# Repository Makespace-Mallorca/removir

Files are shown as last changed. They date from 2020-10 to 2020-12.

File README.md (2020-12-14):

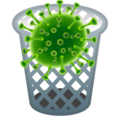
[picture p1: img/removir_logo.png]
#  RemoVir   

## Este repositorio contiene todos los recursos: instrucciones, código, documentación y datos para ayudarte a reciclar un Split (evaporador interior de aire acondicionado) a un eficiente filtro HEPA

Podrás montar un **purificador de aire con filtro HEPA** por poco más del coste de los filtros y lo más importante. Ayudarás a mantener el medio ambiente mientras proteges del contagio de COVID-19 el espacio que más necesites.

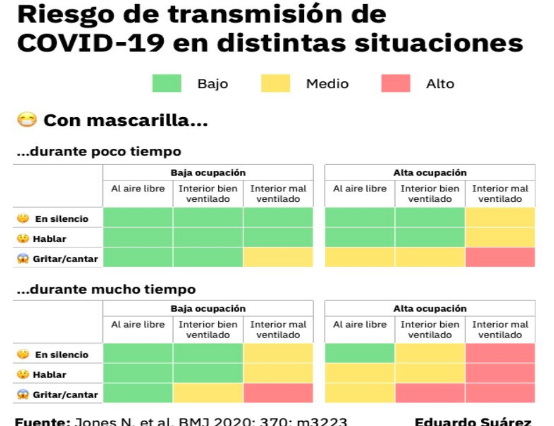
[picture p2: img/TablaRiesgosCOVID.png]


```text
Hemos querido enfocar nuestros esfuerzos a este tipo 
de dispositivos porque creemos que pueden ser una 
importante ayuda a evitar contagios. Las últimas 
evidencias científicas demuestran la transmisión de 
virus por aerosoles, es decir, por el mismo hecho de 
respirar. Esto aumenta el nivel de COV (Compuestos 
Orgánicos Volátiles entre los que se encuentra el 
virus SARS-CoV-2) algo que va correlacionado con la 
concentración de CO2. Esta evidencia hace necesaria 
una correcta ventilación de los espacios cerrados. 
Lo que es tan importante como mantener una distancia 
mínima.
```
<br>
<br>
<br>

Este proyecto parte de la iniciativa de Ernesto Gutiérrez [@erguro1973](https://twitter.com/erguro1973), de [Carlos Orts](https://github.com/McOrts) [@mcorts](https://twitter.com/mcorts) y de los asistentes a varios talleres realizados en el [Fablab de Mallorca](http://fablabmallorca.com/) y organizados por la [Asociación de Makers Mallorca](https://makespacemallorca.org/).

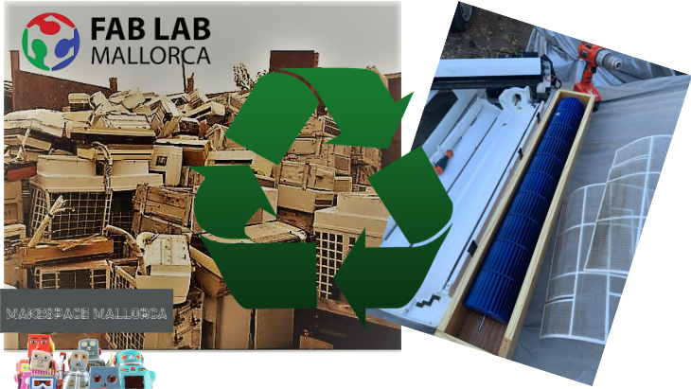
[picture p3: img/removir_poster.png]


**¿Con que vamos a trabajar?**
* Análisis de dinámica de fluidos.
* Control de motores.
* Uso de filtros HEPA.
* Programación C++ e IDE de Arduino
* Microcontroladores ESP8266.
* Sensores
* Comunicaciones MQTT
<br>

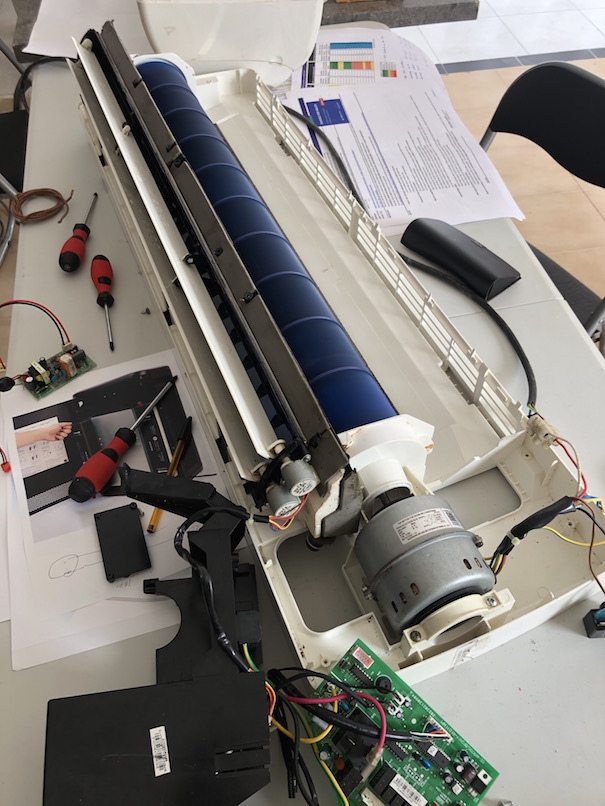
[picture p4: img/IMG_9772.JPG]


## Primer RemoVir, un _Mínimo Producto Viable_
Hemos trabajado sobre un Split marca Mundo Clima. Que ha resultado muy adecuado tanto para la sustitución de la electrócnica como para acomodar los filtros HEPA. Aunque se trata de un MPV. pretendemos que alcance un nivel H13 o superior según el estándar europeo EN 1822-1:2009. para ello se van a instalar 3 filtros HEPA H13 de un equipo profesional Honeywell Incorporaremos un completo sistemas de medición de calidad de aire, CO2, COV, temperatura, humedad y presión atmosférica de manera que sea capaz de adaptar su funcionamiento a las condiciones detectadas.

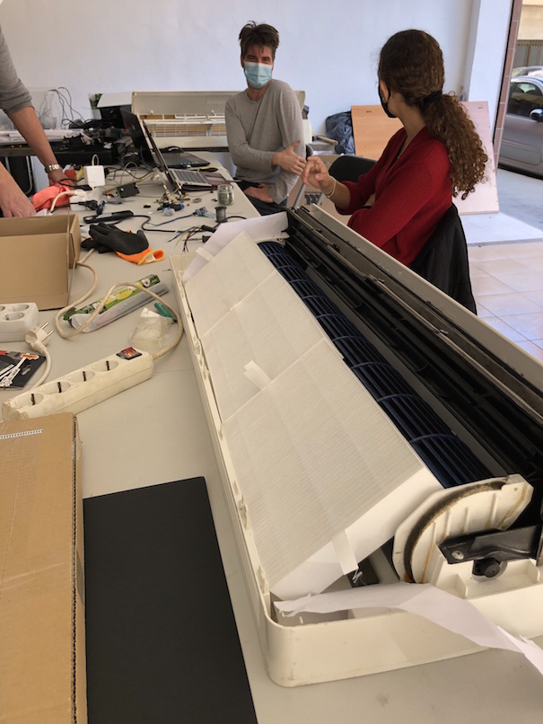
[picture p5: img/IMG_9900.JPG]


### Filtro HEPA (High Efficiency Particulate Air)
Un filtro HEPA funciona con diferentes principios. Lo que determina el comportamiento de la parte impulsora de aire. Una regla básica a tener en cuenta es que una mayor presión de aire puede bajar la eficiencia en la captura de componentes muy pequeños como virus.
El producto elegido ha sido el modelo empleado en el purificador profesional Honeywell H300 que incorpora filtros HEPA de grado H13
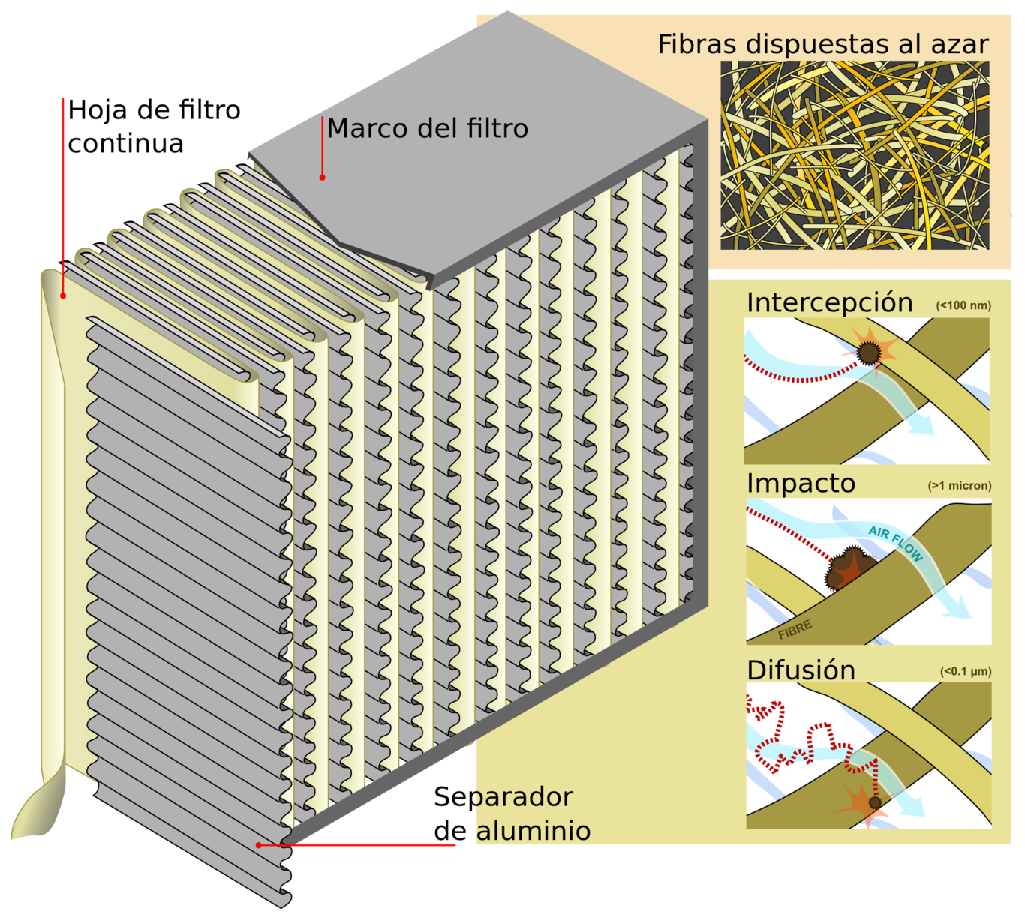
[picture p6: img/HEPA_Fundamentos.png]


### Electrónica
Se ha planteado utilizar el WEMOS D1 MINI Pro. Que es un procesador tipo ESP8266 de 16 bits con programación nativa en C++.
El borrador del esquemático de momento es este:
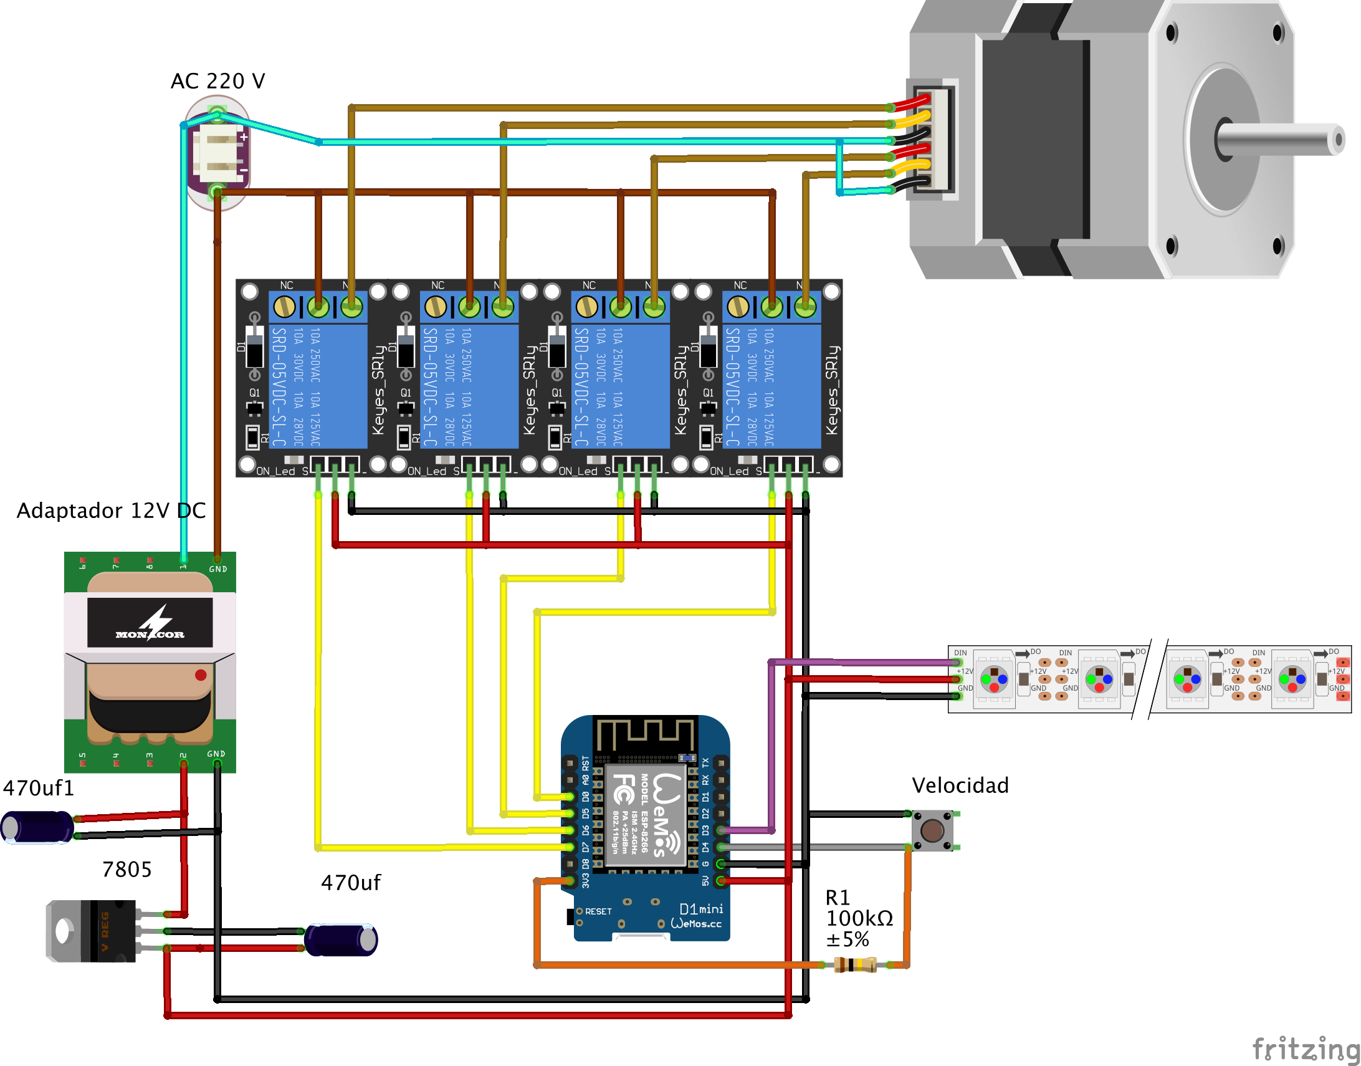
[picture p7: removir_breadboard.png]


### Estructura
Hay que tener en cuenta que detro de un Split encontraremos un ´evaporizador´. A todos los efectos es un radiador de aluminio que sin formar parte de la estructura del aparato. Le confiere uan rigidez estructural que perderemos si no acomodamos los filtros HEPA teniendo en cuenta esta doble función. El diseño de las piezas adicionales evidentemente es una caso diferente para cada modelo. 
Como ejemplo de cómo hacerlo, se han usado patrones en cartulina que luego se han modelizado en SolidWorks para acabar imprimiendolos en 3D de filamento. Los ficheros podéis encontrarlos en este mismo repo.

### Flujo de aire
Este es un concepto que hay que tener presente durante todo el rediseño del equipo. Tanto en el aspecto de caudal como el de presión. Una cosa el el volumen de aire por hora que podamos hacer pasar el equipo y otra diferente es la presión que el ventilador pueda aplicar al aire que mueve. Evidentemente ambos parámetros se ven disminuidos respecto al modelo de aire acondicionado original al sustituir el evaporizador por los filtro HEPA que ofrecen mucha más resistencia al paso del aire.
No está de más valorar las modificaciones haciendo sencillas pruebas de flujo como esta:
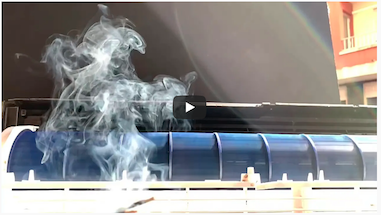
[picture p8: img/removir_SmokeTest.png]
RemoVir RealSmokeTest (https://youtu.be/LHWRh8wFhkA)


### Montaje
El proceso de adaptación y transformación de la mecánica y la electrónica, es algo laborioso y nos ha ocupado algunas semanas. 
* Por una parte hemos tenido que resolver el problema de la sujección mecánica de los filtros en el lugar dejado por el elemento evaporador de aluminio. En un principio de diseñaron soportes imprimibles en 3D par los elementos perpendiculares. Ya que los para las piezas transversales, el material impreso no tienen la rigidez suficiente. Empezamos a utilizar tablero DM que finalmente se ha usado para todo:
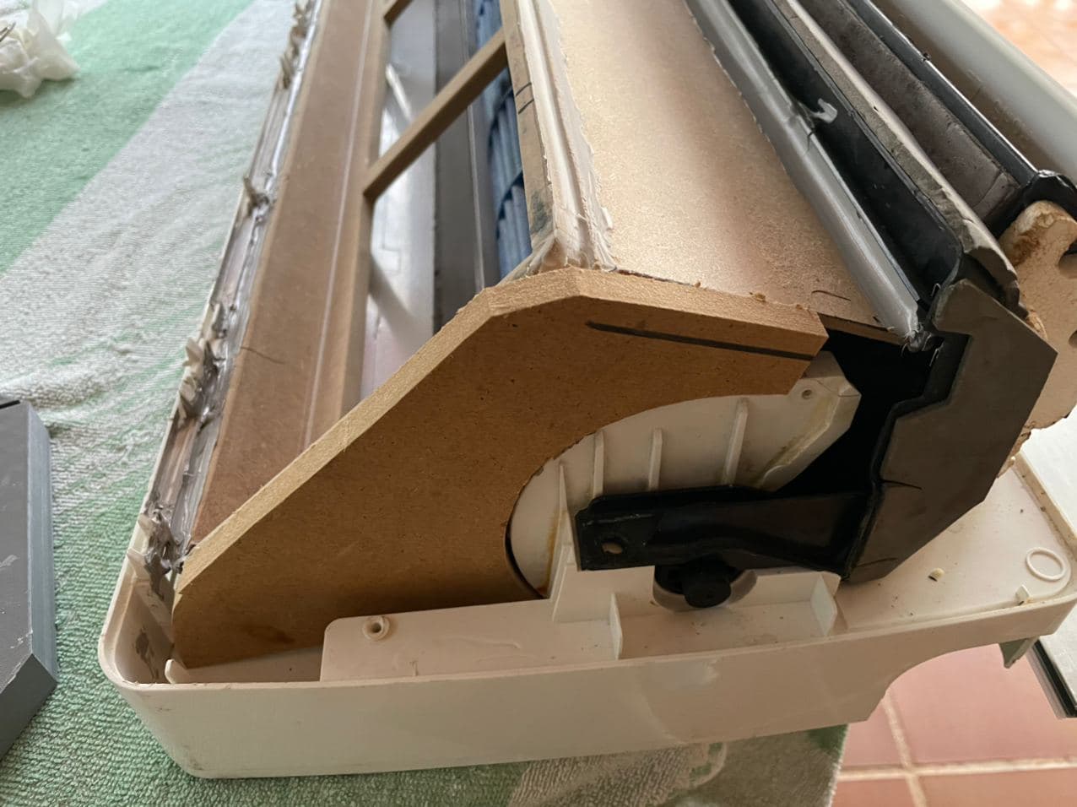
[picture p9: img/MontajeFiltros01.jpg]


* En la parte electrónica se ha utilizado la fuente de alimentación original adaptando la tensión con reguladores de tensión. La lógica está programada en C++ corriendo en un microcesador tipo ESP8266 utilizando las mínimas librerias y un solo bloque de código. Aún así el control se puede hacer desde una página web servida directamente por el micro WEMOS D1 Mini PRO a modo de punto de acceso Wifi.
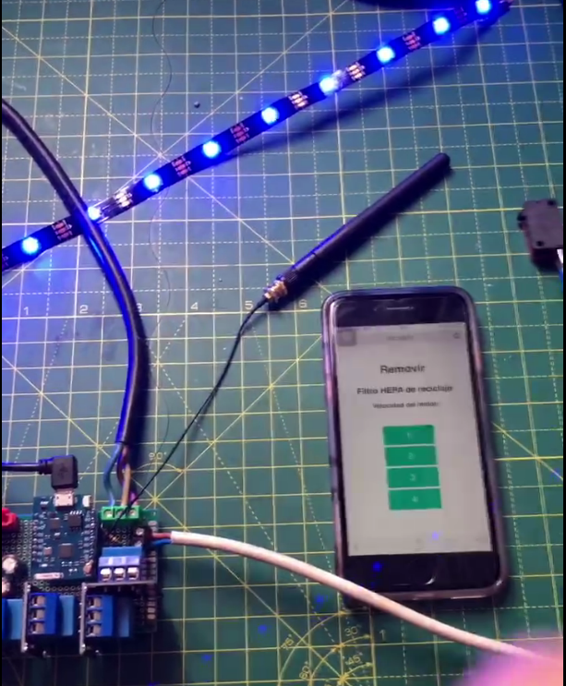
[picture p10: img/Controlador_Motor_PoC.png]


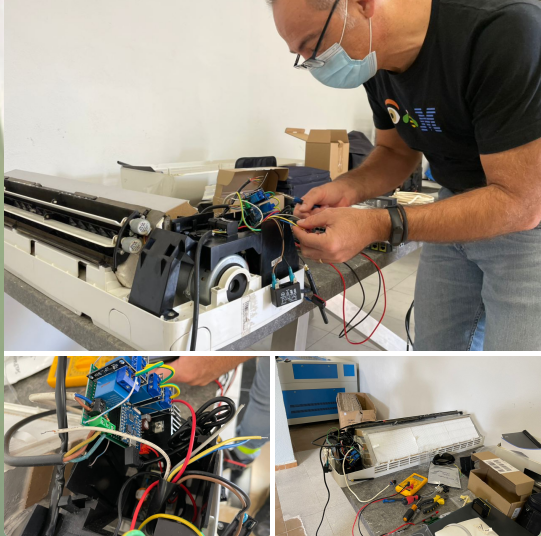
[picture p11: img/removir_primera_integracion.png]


### Primera integración y prueba
El segundo sábado de diciembre, en una de las mañanas de _cacharrero_ organizadas por el Fablab de Mallorca. Hemos integrado todos los componentes y hecho la primera prueba de arranque del motor. Las sensaciones han sido buenas. Un nivel de ruido aceptable así como un caudal de salida de aire aparentemente bueno.
La electrónica parece que está afectada por interferencias que han deshabilitado la conexión wifi en algunos momentos. Y ha detectado falsas pulsaciones en el control manual. Vamos a sustiuir microprocesador, el WEMOS D1 Mini PRO por un WEMOS D1 Mini con encapsulaciento.

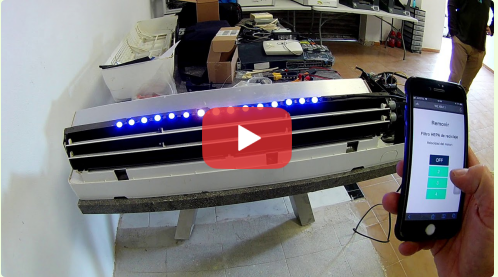
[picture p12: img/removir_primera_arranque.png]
RemoVir primer arranque (https://youtu.be/MKbnKUOGmzY)


### Mediciones y certificación
Como nos gusta saber si el trabajo está bien hecho, y sobre todo, si cumple su función. Una vez instalado mediremos los parámetros de operación como caudal de aire, reducción de COV, etc... para sacar conclusiones sobre mejoras en la siguiente iteracción.
<br>
Llegado el momento vamos a trabajar sobre la conocida hoja de excel de la Universidad de Hardvard que [tenéis aqui](https://github.com/Makespace-Mallorca/removir/blob/main/doc/Harvard-CU%20Boulder%20Portable%20Air%20Cleaner%20Calculator%20for%20Schools.v1.1.xlsx). Considerando esta plantilla se puede realizar el cálculo del CADR ( CLEAN AIR DELIVERY RATE) necesario del purificador, según el tamaño de la habitación, siendo este un parámetro que se indica en todos estos tipos de elementos. Como orientación, para una habitación media de 50m2 y un nivel de renovación bajo sería necesario al menos uno aparato con capacidad de 400 l/min.

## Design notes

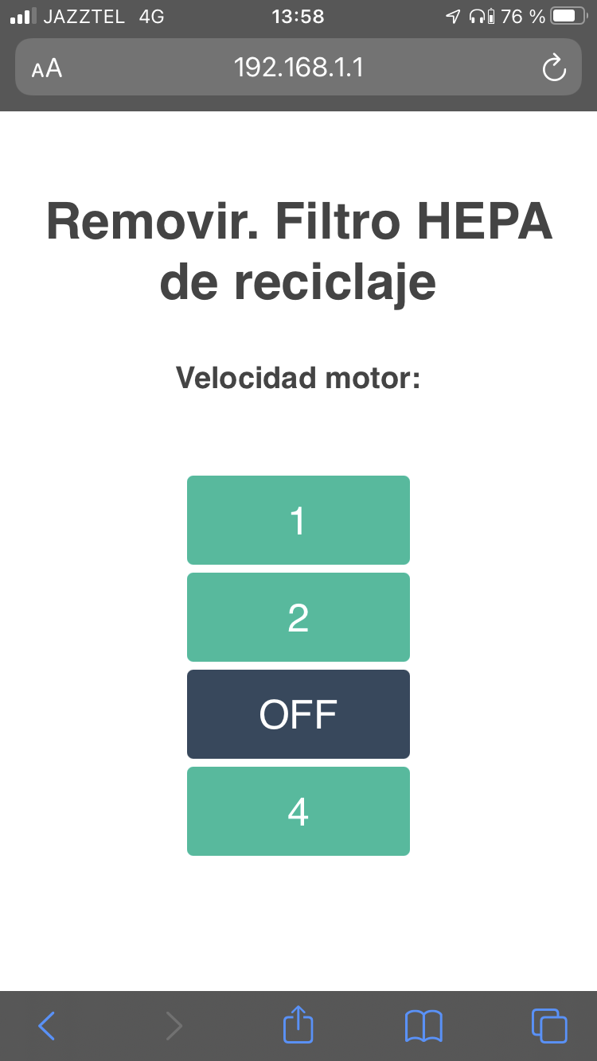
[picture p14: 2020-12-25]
img/Photo 28-11-20, 13 58 09.png

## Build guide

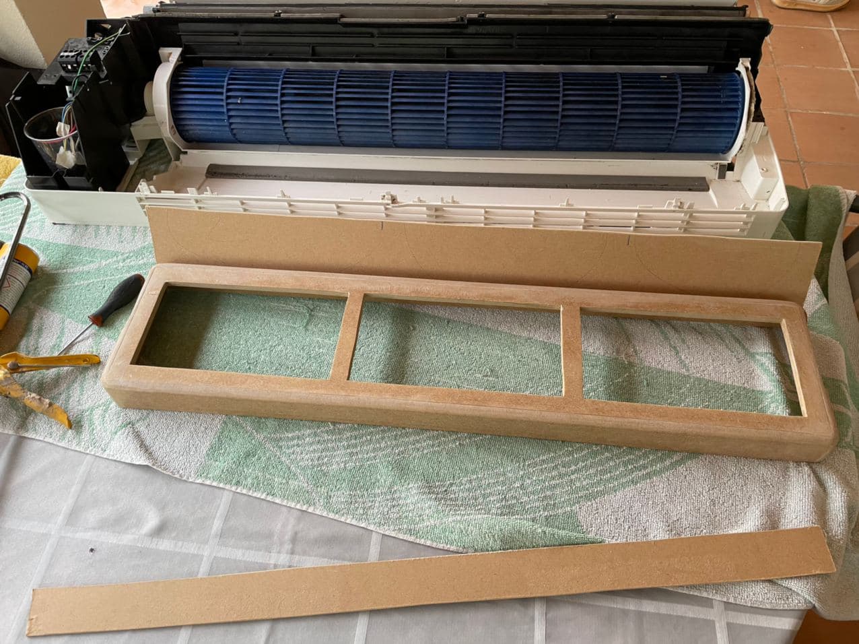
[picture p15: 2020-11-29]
img/MontajeFiltros02.jpg

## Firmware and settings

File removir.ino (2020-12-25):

#include <Adafruit_NeoPixel.h>
#include <ESP8266WiFi.h>
#include <ESP8266WebServer.h>
#include "settings.h"

/* IP direcciones */
IPAddress local_ip(192,168,1,1);
IPAddress gateway(192,168,1,1);
IPAddress subnet(255,255,255,0);

ESP8266WebServer server(80);

/* variables */
int period = 10000;
int time_now = 0;
boolean BotonPulsado = 0;
int velocidad = 0;
int pvelocidad = 0;
bool REL1status = LOW;
bool REL2status = LOW;
bool REL3status = LOW;
bool REL4status = LOW;

/* Configuración led NEOPIXEL */
Adafruit_NeoPixel pixels_STRIP_1  = Adafruit_NeoPixel(NUMPIXELS_STRIP_1, PIN_STRIP_1, NEO_GRB + NEO_KHZ800);

void setup() {
  Serial.begin(115200);

  /* Activación de la wifi */
  WiFi.softAP(ssid, password);
  WiFi.softAPConfig(local_ip, gateway, subnet);
  delay(100);

  server.on("/", handle_OnConnect);
  server.on("/rel1on", handle_rel1on);
  server.on("/rel1off", handle_rel1off);
  server.on("/rel2on", handle_rel2on);
  server.on("/rel2off", handle_rel2off);
  server.on("/rel3on", handle_rel3on);
  server.on("/rel3off", handle_rel3off);
  server.on("/rel4on", handle_rel4on);
  server.on("/rel4off", handle_rel4off);
  server.onNotFound(handle_NotFound);
  
  server.begin();
  Serial.println("HTTP server started");

  /* Iniciar RELEs */
  switch (velocidades) {
  case 4:
    pinMode(PinRele4 , OUTPUT); 
    digitalWrite(PinRele4, LOW );
  case 3:
    pinMode(PinRele3 , OUTPUT); 
    digitalWrite(PinRele3, LOW );
  case 2:
    pinMode(PinRele2 , OUTPUT); 
    digitalWrite(PinRele2, LOW );
  case 1:
    pinMode(PinRele1 , OUTPUT);
    digitalWrite(PinRele1, LOW );
  }
  
  /* Iniciar pulsador */
  pinMode(PinBoton , INPUT);

  /* Iniciar NEOPIXEL */
  pixels_STRIP_1.begin(); // This initializes the NeoPixel library. 
  for(int i=0;i<NUMPIXELS_STRIP_1;i++){
     pixels_STRIP_1.setPixelColor(i, pixels_STRIP_1.Color(0,0,255)); // blue color.
     pixels_STRIP_1.show(); // This sends the updated pixel color to the hardware.
     delay (100);
  }
}

void loop() {
  server.handleClient();

  /* Comandos desde la página web */
  if(REL1status){
    velocidad = 1;
    }
  else {
    if(REL2status){
      velocidad = 2;
      }
    else {
      if(REL3status){
        velocidad = 3;
        }
      else {
        if(REL4status){
          velocidad = 4;
          }
        else {
          velocidad = 0;
        }
      }
    }
  }
  
  /* Comandos desde el botón */
  BotonPulsado = digitalRead(PinBoton);
  if (BotonPulsado == LOW) {
    Serial.println("Boton pulsado");
    velocidad += 1;
    delay (EsperaCambio);    
    if (velocidad == velocidades+1) {
      velocidad = 0;      
    }
  }

  switch (velocidad) {
    case 0:
      REL1status = LOW;
      REL2status = LOW;
      REL3status = LOW;
      REL4status = LOW;
      digitalWrite(PinRele1, LOW );
      digitalWrite(PinRele2, LOW );
      digitalWrite(PinRele3, LOW );
      digitalWrite(PinRele4, LOW );
      break;
    case 1:
      REL1status = HIGH;
      REL2status = LOW;
      REL3status = LOW;
      REL4status = LOW;
      digitalWrite(PinRele1, HIGH );
      digitalWrite(PinRele2, LOW );
      digitalWrite(PinRele3, LOW );
      digitalWrite(PinRele4, LOW );
      break;
    case 2:
      REL1status = LOW;
      REL2status = HIGH;
      REL3status = LOW;
      REL4status = LOW;
      digitalWrite(PinRele1, LOW );
      digitalWrite(PinRele2, HIGH );
      digitalWrite(PinRele3, LOW );
      digitalWrite(PinRele4, LOW );
      break;
    case 3:
      REL1status = LOW;
      REL2status = LOW;
      REL3status = HIGH;
      REL4status = LOW;
      digitalWrite(PinRele1, LOW );
      digitalWrite(PinRele2, LOW );
      digitalWrite(PinRele3, HIGH );
      digitalWrite(PinRele4, LOW );
      break;
    case 4:
      REL1status = LOW;
      REL2status = LOW;
      REL3status = LOW;
      REL4status = HIGH;
      digitalWrite(PinRele1, LOW );
      digitalWrite(PinRele2, LOW );
      digitalWrite(PinRele3, LOW );
      digitalWrite(PinRele4, HIGH );
      break;
  }
  if (velocidad != pvelocidad) {
    Serial.print("velocidad: ");
    Serial.println(velocidad);
    server.send(200, "text/html", SendHTML(REL1status,REL2status,REL3status,REL4status));
    leds ();
    pvelocidad = velocidad;
  }
}

void leds(){
  if (LEDsBinarios) {
    if (velocidad == 0) {
      pixels_STRIP_1.fill(pixels_STRIP_1.Color(0, 0, 0),0, pixels_STRIP_1.numPixels()); // black  
    } else {
      if (velocidad == 1) {
        pixels_STRIP_1.fill(pixels_STRIP_1.Color(0,255,0),0, pixels_STRIP_1.numPixels()); // green  
      } else {
        pixels_STRIP_1.fill(pixels_STRIP_1.Color(255,0,0),0, pixels_STRIP_1.numPixels()); // red 
      }
    }
  } else { 
    if (velocidad == 0) {
      pixels_STRIP_1.fill(pixels_STRIP_1.Color(0, 0, 0),0, pixels_STRIP_1.numPixels()); // black  
    } else {
      if (velocidad == 4) {
        pixels_STRIP_1.fill(pixels_STRIP_1.Color(255, 255, 255),0, pixels_STRIP_1.numPixels()); // white  
      } else {
        for(int i=0;i<NUMPIXELS_STRIP_1;i++){
          pixels_STRIP_1.setPixelColor(i, pixels_STRIP_1.Color(0,0,255)); // blue color.
        } 
        switch (velocidad) {
          case 3:
            pixels_STRIP_1.setPixelColor(2, pixels_STRIP_1.Color(255,255,255)); // blue color.
            pixels_STRIP_1.setPixelColor(3, pixels_STRIP_1.Color(255,255,255)); // blue color.
            pixels_STRIP_1.setPixelColor(11, pixels_STRIP_1.Color(255,255,255)); // blue color.
            pixels_STRIP_1.setPixelColor(12, pixels_STRIP_1.Color(255,255,255)); // blue color.
          case 2:             
            pixels_STRIP_1.setPixelColor(4, pixels_STRIP_1.Color(255,255,255)); // blue color.
            pixels_STRIP_1.setPixelColor(5, pixels_STRIP_1.Color(255,255,255)); // blue color.
            pixels_STRIP_1.setPixelColor(9, pixels_STRIP_1.Color(255,255,255)); // blue color.
            pixels_STRIP_1.setPixelColor(10, pixels_STRIP_1.Color(255,255,255)); // blue color.
          case 1:             
            pixels_STRIP_1.setPixelColor(6, pixels_STRIP_1.Color(255,255,255)); // blue color.
            pixels_STRIP_1.setPixelColor(7, pixels_STRIP_1.Color(255,255,255)); // blue color.
            pixels_STRIP_1.setPixelColor(8, pixels_STRIP_1.Color(255,255,255)); // blue color.
        }
      }
    }
  }
  pixels_STRIP_1.show(); // This sends the updated pixel color to the hardware.
}    
      
void handle_OnConnect() {
  REL1status = LOW;
  REL2status = LOW;
  REL3status = LOW;
  REL4status = LOW;
  Serial.println("handle_OnConnect");
  server.send(200, "text/html", SendHTML(REL1status,REL2status,REL3status,REL4status)); 
}

void handle_rel1on() {
  REL1status = HIGH;
  REL2status = LOW;
  REL3status = LOW;
  REL4status = LOW;
  Serial.println("handle_rel1on");
  server.send(200, "text/html", SendHTML(true,REL2status,REL3status,REL4status)); 
}
void handle_rel1off() {
  REL1status = LOW; 
  Serial.println("handle_rel1off");
  server.send(200, "text/html", SendHTML(false,REL2status,REL3status,REL4status)); 
}

void handle_rel2on() {
  REL1status = LOW;
  REL2status = HIGH;
  REL3status = LOW;
  REL4status = LOW;    
  Serial.println("handle_rel2on");
  server.send(200, "text/html", SendHTML(REL1status,true,REL3status,REL4status)); 
}
void handle_rel2off() {
  REL2status = LOW;
  Serial.println("handle_rel2off");
  server.send(200, "text/html", SendHTML(REL1status,false,REL3status,REL4status)); 
}

void handle_rel3on() {
  REL1status = LOW;
  REL2status = LOW;
  REL3status = HIGH;
  REL4status = LOW;    
  Serial.println("handle_rel3on");
  server.send(200, "text/html", SendHTML(REL1status,REL2status,true,REL4status)); 
}
void handle_rel3off() {
  REL3status = LOW;
  Serial.println("handle_rel3off");
  server.send(200, "text/html", SendHTML(REL1status,REL2status,false,REL4status)); 
}

void handle_rel4on() {
  REL1status = LOW;
  REL2status = LOW;
  REL3status = LOW;
  REL4status = HIGH;  
  Serial.println("handle_rel4on");
  server.send(200, "text/html", SendHTML(REL1status,REL2status,REL3status,true)); 
}
void handle_rel4off() {
  REL4status = LOW;
  Serial.println("handle_rel4off");
  server.send(200, "text/html", SendHTML(REL1status,REL2status,REL3status,false)); 
}

void handle_NotFound(){
  server.send(404, "text/plain", "Not found");
}

String SendHTML(uint8_t rel1stat,uint8_t rel2stat,uint8_t rel3stat,uint8_t rel4stat){
  Serial.print("SendHTML");
  Serial.print(rel1stat);
  Serial.print(rel2stat);
  Serial.print(rel3stat);
  Serial.println(rel4stat);
  
  String ptr = "<!DOCTYPE html> <html>\n";
  ptr +="<head><meta name=\"viewport\" content=\"width=device-width, initial-scale=1.0, user-scalable=no\">\n";
  ptr +="<title>Removir</title>\n";
  ptr +="<style>html { font-family: Helvetica; display: inline-block; margin: 0px auto; text-align: center;}\n";
  ptr +="body{margin-top: 50px;} h1 {color: #444444;margin: 50px auto 30px;} h3 {color: #444444;margin-bottom: 50px;}\n";
  ptr +=".button {display: block;width: 80px;background-color: #1abc9c;border: none;color: white;padding: 13px 30px;text-decoration: none;font-size: 25px;margin: 0px auto 5px;cursor: pointer;border-radius: 4px;}\n";
  ptr +=".button-on {background-color: #1abc9c;}\n";
  ptr +=".button-on:active {background-color: #16a085;}\n";
  ptr +=".button-off {background-color: #34495e;}\n";
  ptr +=".button-off:active {background-color: #2c3e50;}\n";
  ptr +="p {font-size: 14px;color: #888;margin-bottom: 10px;}\n";
  ptr +="</style>\n";
  ptr +="</head>\n";
  ptr +="<body>\n";
  ptr +="<h1>Removir</h1>\n";
  ptr +="<h2>Filtro HEPA de reciclaje</h2>\n";
  ptr +="<h3>Velocidad del motor:</h3>\n";
  switch (velocidades) {
  case 4:
    if(rel4stat)
        {ptr +="<a class=\"button button-off\" href=\"/rel4off\">OFF</a>\n";}
    else
        {ptr +="<a class=\"button button-on\" href=\"/rel4on\">4</a>\n";}
  case 3:
    if(rel3stat)
        {ptr +="<a class=\"button button-off\" href=\"/rel3off\">OFF</a>\n";}
    else 
        {ptr +="<a class=\"button button-on\" href=\"/rel3on\">3</a>\n";}
  case 2:
    if(rel2stat)
      {ptr +="<a class=\"button button-off\" href=\"/rel2off\">OFF</a>\n";}
    else
      {ptr +="<a class=\"button button-on\" href=\"/rel2on\">2</a>\n";}
  case 1:
    if(rel1stat)
      {ptr +="<a class=\"button button-off\" href=\"/rel1off\">OFF</a>\n";}
    else
      {ptr +="<a class=\"button button-on\" href=\"/rel1on\">1</a>\n";}
  }
  ptr +="</body>\n";
  ptr +="</html>\n";
  return ptr;
}

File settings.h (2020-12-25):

/* Configutraciones del Removir */

// SSID y clave de la wifi que sirve 
const char* ssid = "Removir";
const char* password = "12345678";

// MOTOR 
const int velocidades = 2; // de 1 a 4
const int PinRele1 = 13;
const int PinRele2 = 12;
const int PinRele3 = 14;
const int PinRele4 = 16;

// LEDs
const int PIN_STRIP_1 = 0;
/* Velocidad 1=verde, 2=rojo */
	const bool LEDsBinarios = true;
	const int NUMPIXELS_STRIP_1 = 1;
/* Escala de blanco sobre azul 4 velocidades */
	//const bool LEDsBinarios = false;
	//const int NUMPIXELS_STRIP_1 = 15; // No modificar

// Otros parámetros
const int EsperaCambio = 1000; //milisegundos
const int PinBoton = 2;

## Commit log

2020-11-29 Versión MVP
    [removir_breadboard.fzz]
2020-12-25 Añadido fichero configuración
    Se pueden parametrizar el número de velocidades del motor de 1 a 4 y el modo de funcionamiento de la tira de NeoPixel.
